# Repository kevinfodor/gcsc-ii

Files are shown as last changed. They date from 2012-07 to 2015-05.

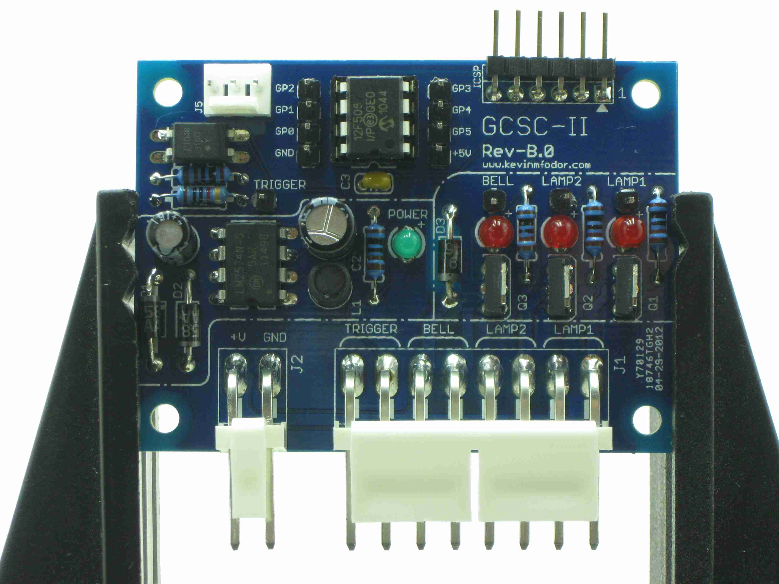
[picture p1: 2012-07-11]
images/gcsc-ii_pcb_assembled_sm.jpg

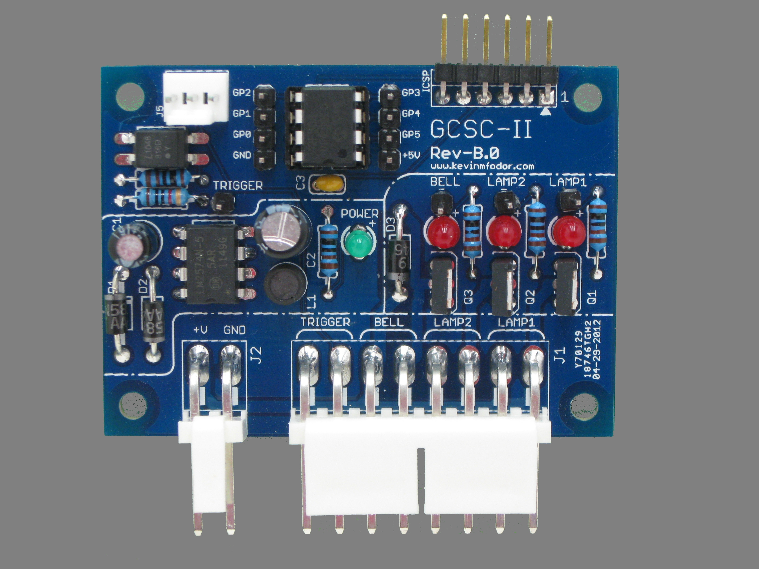
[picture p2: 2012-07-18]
images/wiki/gcsc-ii_pcb_front_grey.jpg

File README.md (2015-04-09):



This is a small embedded controller designed for the purposes of controlling an operating railroad crossing signal with 2 signal lamps and a bell. It was designed to work with a PVC based railroad crossing signal mast approximately 6-feet tall for display, demonstrations and overall amusement. I  have posted this design because I have been contacted by a few others who also saw my railroad crossing project and expressed a desire to build such a signal themselves. I hope this controller will be helpful to anyone who wishes to look at it.

This site contains all of the documentation, source code, schematic and PCB files necessary to build this controller (Rev.B). Please seek the Wiki for more details.

As a secondary goal, I also designed this board to be used as a PIC12 development board. The PCB silkscreen is well documented showing all the pin names and contains lots of holes for jumpers. The board can also be used directly with the PICKit3 programmer from Microchip via the ICSP header. It also has it's own 5V switching power supply on board. So basically all you need to do is provide power and your off and running.

In case your wondering about all the mention of "II" as in GCSC-II, this is a complete re-design of my earlier breadboard attempt found [here on my site](http://www.kevinmfodor.com/home/model-railroading-projects/railroad-crossing-signal). Much has changed since then. This is a very easy to build and very low-cost implementation of that control circuit.

I hope people find this useful. Please feel free to email me or contribute in anyway.

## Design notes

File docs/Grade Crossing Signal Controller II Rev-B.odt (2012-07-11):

# Grade Crossing Signal Controller II

Revision B

Requirements, Design and Implementation

Written By: Kevin Fodor

www.kevinmfodor.com

## Background

Recently someone was interested in my Railroad Signal Crossing Project (http://www.kevinmfodor.com/home/model-railroading-projects/railroad-crossing-signal) posted on my projects web site. He intends to build his own barrel-car train which will be able to pull around kids which should prove to be a huge amount of fun for them. Being of a train theme he was interested in constructing four grade crossing signals (crossbucks) presumably to lay about the area where the barrel cars would follow. Seing my project on my website he contacted me for more detailed plans on the construction of the signal post itself as well as the electronic controller for the lights and bell.

The physical construction went well and he made a great deal of improvements to make it easier to construct the signal itself. The electronics however were a bit more challenging. My original design was cobbled or hacked together as a work-in-progress. This means I didn’t set out to design anything. Just kind of put enough components together (wire-wrapped) and debugged the circuit till it worked. Consequently other than the schematic which documents the circuit, there is very little information on how to actually duplicate the circuit (wiring points, etc.). Of course my intent was never to make more than one one them anyway. Now that there is interest in making more than one, a better plan and approach is required.

## Purpose

This document will serve as a collection of objectives, requirements and design notes accumulated overtime to guide the re-design of this controller.

### Current Design Weaknesses

The re-design is aimed at making the controller simpler to build and more reliable among many other things. To address what improvements are to be made, below are the weaknesses I see in the existing controller desing;

- The existing design is wire-wrapped onto proto-board. This makes it very difficult to debug, copy and maintain as wires are fragile and break easily. Additionally, connection points are not easily observed.
- Overall the part count is rather high for what should be a very simple circult.
- The existing design uses a 556 (dual 555) timer to both trigger the signal (and control the on time) as well as the astable operation of the lights and bell. These devices are notoriously problematic and I have found often false trigger if great care is not observed. Additionally to obtain a square wave pulse (50% duty cycle) a diode is required, adding to the part count.
- The power output for the lights and bell are based on power transistors (TIP31 and TIP120). Although they appear to do the job, they are not very efficient and require drive transistors to operate them. They are also more difficult to use and generate significant heat while operating.
- The bell signal is derived from light flashing signal (derivative of the square wave using a diode, D2 and D3). This adds to the number of component required and complexity. More importantly however this also makes timing the bell “strike” time somewhat tricky as it is subject to the RC circuits (C9, R10) and (C10, R11). Along with the drive circuits, these parts are duplicated for each clock edge to trigger the bell.
- Separate transformers were needed since the bell being an inductive load tended to drop the supply voltage to the timer and other circuitry causing all sorts of “drop-out” problems. Transformers are expensive and it would be nice to require only one, and only if being powered by AC household line current. Each transformer also required a diode bridge to rectify the AC signal, duplicating those parts as well.
- The power supply is a linear one based on the LM7812 (Q1) which again is quite inefficient and not really suited to supply large currents to the lamps and bell.
- This board is a one-of-a-kind (sigh!) and making another is quite difficult (and expensive). If others would like to make them it is difficult to convey how to build it and to do so it would take some skill and patience.

## Design Goals

With the above listed and numerous weaknesses in mind, the following design goals are set in order to address them;

- The hardware design should use commonly available (free) tools which make the design open and accessible to others who may want to build and or modify the design further.
- Building a copy of the circuit should be simple, enabling many people of all kinds of skill level to build one. With this in mind a Printed Circuit Board (PCB) will be produced using through hole components.
- Overall part count to be reduced by 50%. Current design uses about 50 parts!
- Reduce overall cost to build. Current design costs $x to build.
- Trigger type and duration of signal operation shall be flexible (i.e. via software)
- Flash cycle time should be flexible (i.e. via software). However, as a baseline the previous design ran at 0.722 Hz with a 50% duty cycle (693 msec on/off) time so we will start with that.
- Bell Trigger time should be flexible (i.e. via software). Again since the previous design triggered the bell on each flash of the lamp, the bell will be triggered every 693 msec.
- Power stage should use more efficient power switching components (i.e. MOSFETs)
- Power supply shall be more efficient and provide enough power to lamps and bell (i.e. switching power supply)
- Software will control operation making it much more flexible to all users. Thus the controller will be based on a small and inexpensive microcontroller.
- Optional household AC or battery powered. This is due to the fact that unit may be used outdoors or where AC line current may not be available. In fact it is better to simply design the circuit to use DC power then add a AC->DC converter if needed.
- Learn something!
- Make it better!

## Block Diagram

The block diagram below shows the overall control circuit as a black box. What is inside the black box is what needs to be re-designed.

Illustration 1: Controller Block Diagram

## Physical Requirements

To meet the design goals set forth earlier, some physical requirements must be met;

1. Unit will be powered by a 12-VDC (nominal, 13.6 actual) battery
  a. Input power supply may vary between 9-VDC and 18-VDC and thus power supply should be tolerant of that.
  b. Target battery is a commonly available motorcycle/tractor battery (specs?)
    i. Consider small motorcycle battery with 3Ah capacity. High capacity are 14Ah capacity.
    ii. Power Wheels batteries are typically 9.5Ah SLAs.
    iii. 9V Duracell Copper Top, 10mA load over 50+ hours.
  c. Idle, quiescent current consumption should be less than 10mA.
2. Unit will include reverse polarity protection as to not blow out the controller if battery voltage is applied incorrectly.
3. Power supply will indicate operation using an LED.
4. Unit will be designed to anticipate being placed in a small enclosure (water resistant if used outdoors)
5. Must be able to independently control two automotive tail-light bulbs.
  a. May support either single or double filament bulbs
    i. Tail/marker Filament 12-VDC @ 0.5 A
    ii. Signal Filament 12-VDC @ 2.0A
6. Must be able to actuate a bell (Ace #36487 (http://www.acehardwareoutlet.com/productdetails.aspx?sku=36487))
  a. Note! This bell is a self-interrupting circuit as purchased. A modification must be made to the bell to allow it to work as a bell in this project and not as a “door-bell”. See Section 4 for more details.
  b. Bell is typically powered using three 6V DC batteries or AC-125C/36485 transformer (http://www.acefactorystore.com/proddetail.asp?prod=36485) (Output: 8 VAC-10 VA, 16 VAC-10 VA, 24 VAC-20 VA).
7. Must be triggered by a momentary switch.
8. Support a low-power mode when not in operation.
9. Diagnostic LEDs should be included for each lamp and bell to verify operation if such devices are not connected.
10. PCB and wiring harness should use commonly available wire-to-wire connectors suitable for outdoor environments.

## Functional Requirements

The unit has very few functional requirements. Those requirements are detailed below.

1. Trigger – Actuates the grade crossing signal controller, causing lights to flash and bell to ring along with general amusement by all.
  a. Momentary actuation via push button or make/break connection.
  b. Toggles signal on/off
    i. Press once to turn on, press again to turn off
      1. Maximum on time is 30 seconds (timeout)
    ii. Hold for continuous operation (> 2 seconds)
      1. No timeout (forever).
      2. Turn off if pressed again.
2. Lamps (2)
  a. 12-VDC Automotive Taillight Lamps (0.5/2.0 Amps)
  b. Flash at an approximate 2/3 second rate, 50% duty cycle.
3. Bell
  a. 12-VDC Door Bell (modified, 2-3 Amps peak pulse driven)
  b. Strike bell in sync with each lamp flashing
  c. Strikes are generated by short pulse to bell.

## Trigger Design

The trigger is the only control input into the signal controller. It provides several functions although it is only a single momentary switch. To adequately define this behavior it is often helpful to develop a finite state-machine.

Modes: Active (Timeout, Continuous), Inactive

## Stock Bell Modifications

The signal’s bell which is to be used is a commonly available door-bell (Ace #36487 (http://www.acehardwareoutlet.com/productdetails.aspx?sku=36487)) available at most hardware stores. The bell, as it comes stock in the package is actually made from an electromagnet which is used to operate a self-interrupting circuit (http://home.howstuffworks.com/home-improvement/repair/doorbell2.htm). This is useful when operated from a line transformer (as is intended), but for our purposes the controller circuit will be actuating the bell instead through a short pulse. To do this, we will need to modify the bell slightly.

Here is an illustration of the door-bell as it is provided. Understanding its operation as a self-interrupting circuit is helpful so that we can understand how to modify it properly.

A C B

When electromagnet

is not engaged circuit

is complete

Illustration 2: Door bell (unmodified) when circuit is closed.

One end of the electromagnet wire is connected directly to one end of the electrical circuit (terminal-C). The other end of the wire connects to a metal contact, which is adjacent to a moving contact arm or clapper (terminal-A). The clapper is a thin piece of light, conductive metal. The anchored end of the clapper is wired to the battery (terminal-B). When the electromagnet is turned off (Illustration 2 above), the free end of the clapper rests against the contact point (terminal-A). This forms a connection between that end of the wire and the electrical circuit. In other words, electricity can flow through the electromagnet when the circuit is closed (terminal-A and B are connected).

A C B

Bell strike when electromagnet

is engaged, but circuit is broken

releasing the arm again

Illustration 3: Door bell (unmodified) when circuit is open

Initially, the electromagnetic field attracts the clapper off the stationary metal contact (terminal-A). This breaks the connection between the circuit and electromagnet, so the electromagnet shuts off (Illustration 3 above). Without a magnetic field pulling it back, the clapper snaps back into position against the stationary contact (terminal-A). This reestablishes the connection between the electromagnet and the circuit, and the current can flow through it again. The magnetic field draws the clapper up, and the process repeats itself as long as you apply power from the battery. In this way, the electromagnet keeps shutting itself on and off. The ringing sound you hear is the sound of the rapidly moving clapper hitting the bell dozens of times a second.This is the same system used in old-fashioned fire alarms and school bells.

This is all very interesting but it is not the behavior we want. What we want is to be able to control the bell enough to achieve a single strike of the bell each time a lamp is turned on. To do this we need to modify the stock door bell so that it is now a non-interrupting circuit. The single strike will instead be controlled by our controller.

A C B

add jumper

Illustration 4: Door bell (modified) as a non-self interrupting circuit

In Illustration 4 above we can see that by adding a jumper between terminal-A and terminal-B we effectively disable the self-interrupting part of the circuit. Now applying the power source to the circuit causes the clapper to strike the bell. Keep in mind with this modification, as long as power is applied, the electromagnet is engaged and the bell is struk. The clapper arm will not move away from the bell until the power source is removed. It is this operation that our controller is responsible for. The controller must be able to apply the power source to the circuit as a quick pulse, just enough to ring the bell once and then disengage. To determine just how long to pulse the circuit was unknown, so a test circuit needed to be designed.

## Bell Driver Test Circuit

The bell driver portion of the design was always the most troublesome for me, so let's start there. Once we have that designed the rest should be a piece of cake.

The bell we are going to design the output circuit for is an Ace #36487 (http://www.acehardwareoutlet.com/productdetails.aspx?sku=36487). It consists of an electromagnet (coil) which must be stimulated with a voltage to make the arm move. The moving arm is attached to a long clapper, which rests alongside a circular bell. When the arm is moved (current applied) it strikes the bell. When current is removed the arm moves away from the bell (snaps back) ready to strike again.

The specs on the door-bell state that it can be driven with three 6V DC batteries (18 VDC) or AC using the 125C/36485 transformer. Since our controller uses DC voltage (supplied by a 12 VDC battery) we will use 12 VDC to drive the bell. It has been found that the bell can be adequately driven using 12 VDC.

Moving the arm with the electromagnet is problematic because it is what is known as an inductive load. So some extra considerations need to be made when driving an inductive load versus and purely resistive one (such as a lamp). One thing to note is that the coil resistance at steady state is approximately 3-4-ohms. At steady state, with 12 VDC applied, this means the current through the coil would be as high as 4 amps. That also means the bell could draw as much as 36 watts! That is a significant amount of power. With power comes heat, and if you apply that current for too long the bell's coil will burn out.

Fortunately for us we actually don’t want to drive the bell’s coil with a steady current. In fact doing so would slam the arm against the bell and keep it there. There would not result a “free ringing” sound and instead it would be muffled by the arm resting against the bell. Instead we want a quick, bright ring when we trigger it. We can do this by driving a short pulse into the bell.

So how long should the pulse be? What will be the current through the bell during that time?

To answer this we need to experiment. A sample test circuit to determine this was constructed as in Illustration 5. This circuit allows me to send a pulse (from a microcontroller) into the bell driver circuit and view on an oscilloscope how much current is going through the bell. Current is measured across Rref which is a 1Ω 10-Watt Power resistor.

Illustration 5: Bell Coil Driver Test Circuit

To stimulate the bell, I drive a periodic (1-second) pulse of approximately 10 msec in width through the coil. Probing across Rref shows the current through the 1Ω resistor. At this point the math is easy as we simply use V = I*R given Rref = 1Ω, we then know the voltage is equal to the current through the resistor V=I.

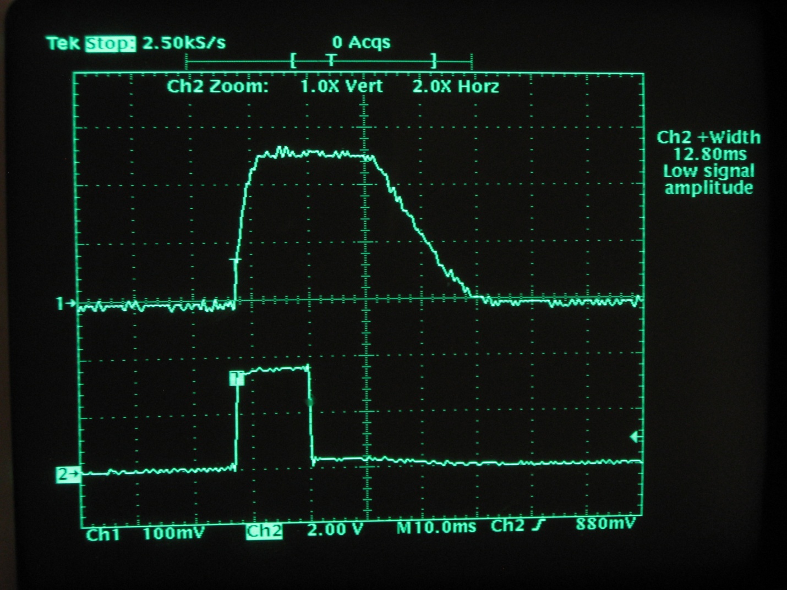
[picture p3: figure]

Illustration 6: Experimental Bell Driver Test Circuit Trace

The trace is shown above in Illustration 6 as seen on the oscilloscope. The microcontroller generates a 12.80 msec pulse to drive the opto-isolator which drives the MOSFET gate. The current through the coil is the same as that which is through the MOSFET drain-source and the Rref resistor. As can be seen from the trace, The initial current starts at 0 and increases exponentially to 2.6-Amps, after about 4 msec reaches steady state, and then about 25 msec after the pulse goes low it begins to exponentially decrease back to 0 amps after about 43 msec total.

To simplify let’s just assume with an approximate 10 msec pulse, the device sees full current for 50 msec every 700 msecs. Also recall that the 1Ω resistor, Rref won’t be in the actual drive circuit (it was only used for these measurements), so we have to assume the maximum current which we have seen at 12V, steady state which is about 2.75 A.

With this information we then know that at 12 VDC, the bell sees 2.75A for less than 10% of the time. This is worst case scenario and will serve as guidance into our design process for the bell driver.

## Basic Design Elements

The overall circuit consists of 4 basic sections or elements which are 1) High Power Output Stage, 2) The Controller 3) Trigger and 4) Power Supply. Each of these elements are addressed below.

### High Power Output Stage

The high power output stage needs to drive two lamps and a bell. So we need three separately and digitally controlled high-power output control circuits. Since the microcontroller will be controlling and thus driving each circuit, the circuit must be controllable using a +5V signal. We also must consider power dissipation of the control circuit itself. We are switching (worst case) 2A of current to each lamp. Designs for the lamps and bell will be addressed separately below.

Often the first solution a design reaches for when needing to switch high power loads with a microcontroller or other small voltage and current device is a relay. However relays are notoriously unreliable in an outdoor environment, involve mechanical parts and will require drive circuitry of its own anyway since a microcontroller cannot on it's own drive the relay's coil.

Another approach is to use bipolar transistors. This is the approach I took on my first design (http://7450666183147974826-a-1802744773732722657-s-sites.googlegroups.com/site/kfodorprojects/home/model-railroading-projects/railroad-crossing-signal/Visio-C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) using a TIP31 (http://www.fairchildsemi.com/ds/TI/TIP31A.pdf) for the lamps and Darlington TIP120 (http://www.fairchildsemi.com/ds/TI/TIP120.pdf) for the bell. It also required a small NPN transistor to drive each of them. In total 16 parts (resistors and transistors) were needed to implement the circuit. Furthermore these transistors are current controlled devices requiring a significant base current to turn them on. Additionally the lowest attainable on-state voltage drop is determined by the collector-emitter saturation voltage VCE(SAT), which for the TIP31 VCE(SAT) = 1.2 V when IB = 375mA, while the TIP120 VCE(SAT) = 2.0 V when IB = 12mA. Power dissipation (which is converted to heat) is determined by P = VI so the heat generated by the part is subject to this VCE(SAT) parameter. Using the TIP31 to drive a 2A lamp results in a best case power dissipation of 2.4 watts (a 0.5 A load dissipates 0.6 watts). That best cast occurs when driving the base with 375 mA. A TO-220 package has a typical thermal resistances of TR(j-c) = 3 ºC/W and TR(c-a) = 62.5 ºC/W. Thermal resistance is an important parameter because it determines how high the temperature of the device will rise when dissiping an amount of power. Of specific importance here is the device's junction temperature (Tөj), which for the TIP31 cannot exceed 150 ºC. Plugging those values into the basic device thermal characteristic equations is as follows;

T_"R(j-a)" = T_"R(j-c)" + T_"R(c-a)" = (3 + 62.5) %degree C/W = 65.5 %degree C/W
newline
newline
T_rise = T_"R(j-a)" cdot P_D = 65.5 %degree C/W cdot 2.4 W = 157.2 %degree C
newline
newline
T_rise = T_"R(j-a)" cdot P_D = 65.5 %degree C/W cdot 0.6 W = 39.3 %degree C

Woah! At an ambient temperate of 25 ºC the 2A lamp causes the TIP31 junction temperature to be about 182.2 ºC (360 ºF). That is 32.2 ºC above the maximum. The 0.5A lamp will make it about 64.3 ºC (148 ºF) which is within the limits. So, the 2A load is simply not possible (the transistor will blow) and the 0.5A load is still pretty hot. I am glad that this transistor is on only half the time! I have noticed that in the original prototype circuit these lamp drive transistors were pretty hot at the 0.5A load, I never tried a 2A load. Glad for that!

For the re-design I chose to use MOSFETs. MOSFETs are great for switching high currents because they are voltage controlled devices and if driven properly have a very low “on” resistance known as RDS(ON). Low “on” resistance means more efficiency, less power dissipation and therefore less heat. There are other choices as well (i.e. IGBTs for instance) but I decided on MOSFETs since much of this work would also be a basis for other work I would like to do in the area of motor controllers. So I went with MOSFETs.

There are some important considerations to take into account when driving MOSFETs however. One is the gate drive voltage, VGS, the other is switching speed.

MOSFET based power designs can gain additional efficiency by properly matching the gate drive voltage VGS with the MOSFETs being driven. Driving a MOSFET gate with a higher voltage, results in lower on-resistance, RDS(ON). However we cannot drive the MOSFETs with too high of a gate voltage without requiring additional drive (level translation) circuits which again add cost (the BOM) and complexity (the PCB layout). Higher gate drive voltage levels place additional charge into the gate-to-source junction of the MOSFET, resulting in increased losses within the MOSFET driver stage. To increase efficiency the applied voltage should drive the MOSFET gates such that the added gate charge and switching losses are less than the power savings gained by lowering the RDS(ON).

Higher gate drive results in higher switching losses when used at higher frequencies, switching losses dominate in which case a lower VGS would be preferred. At lower frequencies, where conduction losses dominate, a lower RDS(ON) is preferred, and higher VGS is desired. The consideration for switching speed is not really an issue in this application. The lamps are not driven faster than being turned on or off every 0.7 seconds ( < 1.5 Hz). The bell is switched on and off a bit faster, but infrequently, once every 0.7 seconds it is switched on for 10 msec then switched off. Even if this were continuous it would only be at a rate of about 100 Hz. At those frequencies switching speed really is not significant. It usually isn't a factor with MOSFETs till we start talking about several kHz switching speeds.

In this application, the controller has a 5V output so ideally being able to drive a MOSFET at a VGS of 5V is desired.

Another consideration is weather to use a low-side or high-side driver configuration.

A low side driver is implemented with the switch (N-Channel MOSFET) between the device being controlled and ground. A high side driver is implemented with the switch (P-Channel MOSFET) between the +V supply and the device. These two types are shown below.

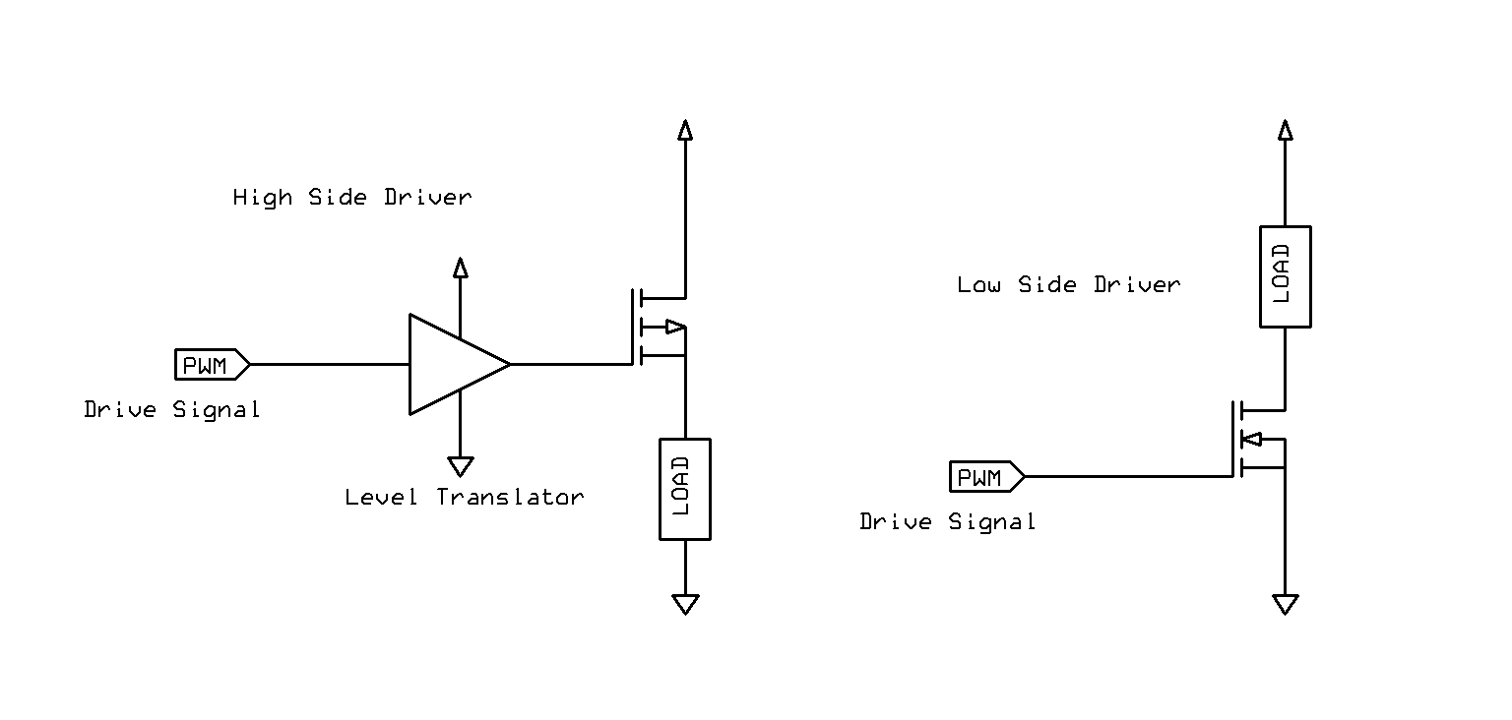
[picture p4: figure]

Illustration 7: Comparison of High-Side and Low-Side Drivers

Low-side drivers in some applications are considered somewhat “less safe” because the device has voltage on it even when turned off. For instance, what is someone cuts the cable or damages the device and it shorts to ground. Additionally since the load is hot, it can be turned on without the controller by connecting the opposite side to ground. If this were a motor for instance, the motor could be accidentally turned on.

High-side drivers are preferred from a robustness and sometimes safety perspective. This is particularly important when the device being driven is not near the controller. When the high-side driver is off, the device is at ground potential, with little or no current flow. However, high-side drivers are somewhat more complex to implement and require more components (i.e. drivers, level translators), especially when the logic level driving them doesn't match the driver voltage.

In this case a low side driver was implemented for its simplicity and reduced complexity (shown below). The driver (without LED state indicator) consists of only two parts. The MOSFET, Q switch and bleeder resistor RB. An LED diode, D and current limiting resistor RA were added to given visual indication of the switch state which is helpful during development and troubleshooting. It also allows the circuit to be useful even without a load connected to the output.

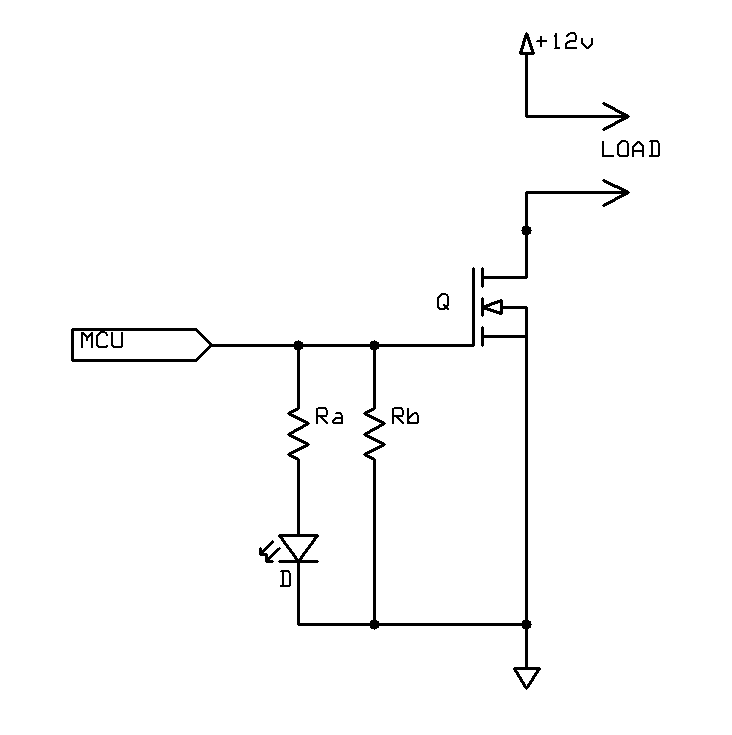
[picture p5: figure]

Illustration 8: Basic Power Output Low-Side Driver Circuit Design

The bleeder resistor, RB is used to bleed off current from the MOSFET gate when not being driven. A MOSFET gate acts much like a small capacitor which can leave a charge (and thus leave the switch on) when not being driven. A value of 100kΩ was chose for this resistor which draws a maximum of 50µA. In fact the bleeder resistor is probably not even needed in this application since it is connected to a microcontroller output pin. A bleeder resistor is only really needed when the input maybe left floating.

Note: I plan on removing the bleeder resistors in the next revision of the board.

The indicator circuit made up of a red LED, D (SSL-LX5093HD) and current limiting resistor RA = 1kΩ sets the LED current at about 3 mA due to the LED's forward voltage drop of VF = 2 V. See Section 'Power Supply Design' below. This is sufficient current to drive the LED.

MOSFET Q was selected as an On-Semiconductor NTD4906N-1G (http://www.onsemi.com/pub_link/Collateral/NTD4906N-D.PDF) N-Channel Power MOSFET. The characteristics of this MOSFET are low RDS(ON), low gate capacitance and relatively small through-hole package (IPAK). At $0.26/ea they are very inexpensive.

Absolute Maximum Ratings at TA = 25ºC

VDSS = 30 V

VGS = +/- 20 V

ID = 10.3 A (continuous, no heatsink or pad)

PD = 1.38 W

TӨj = 175 ºC

Electrical Steady State Characteristics

RDS(ON) = 7 mΩ at VGS = 4.5 V

RDS(ON) = 6 mΩ at VGS = 5.0 V

TӨ(j-a) = 109 ºC/W

It would be perhaps considered “better-design” to have implemented a high-side driver instead. But its not like we are dealing with big heavy motors here. So I went with the simpler design approach.

### Lamp Output Stage Design

Note: Most automotive trailer bulbs have two terminals each connected to a different filament. One for turn signal (green wire) and another for taillight (brown wire). They are both referenced to the chassis ground or frame via a bolt. The turn signals draws approximately 2A while the taillight draws 0.5A. I have used both terminals and obviously one is significantly brighter than the other. Since this is likely to be used outdoors, the brighter one is considered in the design. Also since this would also represent the worst case scenario, the 2 A filament is used for that reason as well.

Using ID = 2 A, and TӨ(j-a) = 109 ºC/W we calculate power dissipation, junction temperature rise and expected junction temperature in ambient conditions TA = 25 ºC.

P_D = I_D ^ 2 cdot R_"DS(ON)" = (2A)^2 cdot 0.007%OMEGA = 0.028 W = 28 mW
newline
newline
T_rise = T_{%THETA(j-a)} cdot P_D = 109 %degree C/W cdot 0.028 W = 3.052 %degree C
newline
newline
T_{%THETA j} = T_a + T_rise = 25 %degree C + 3.052 %degree C = 28.052 %degree C

Both power dissipation, PD = 28 mW and junction temperature TӨj = 28 ºC (83 ºF) are well below this MOSFETs maximum ratings, PD(max) = 1.38 W and TӨj(max) = 175 ºC. These results are also much better than the original transistor based design.

### Bell Output Stage Design

Using ID = 2.75 A, and TӨ(j-a) = 109 ºC/W we calculate power dissipation, junction temperature rise and expected junction temperature in ambient conditions TA = 25 ºC.

P_D = I_D ^ 2 cdot R_"DS(ON)" = (2.75 A)^2 cdot 0.007%OMEGA = 0.05294 W = 52.94 mW
newline
newline
T_rise = T_{%THETA(j-a)} cdot P_D = 109 %degree C/W cdot 0.053 W = 5.77 %degree C
newline
newline
T_{%THETA j} = T_a + T_rise = 25 %degree C + 5.77 %degree C = 30.77 %degree C

Both power dissipation, PD = 53 mW and junction temperature TӨj = 30.77 ºC (87.39 ºF) are well below this MOSFETs maximum ratings, PD(max) = 1.38 W and TӨj(max) = 175 ºC.

This circuit is identical to the lamp output stage expect for the fact that a “freewheel, flyback, or snubber diode (http://en.wikipedia.org/wiki/Flyback_diode)” is needed in a reverse biased direction across the bell's coil. This helps to eliminate the sudden voltage spike seen across an inductive load when its supply voltage is suddently removed. When the device rapidly turns off, the diode becomes forward biased and the collapse of the energy stored in the coil causes a current to flow through the freewheel diode. Without this protection in place high currents would occur causing a high voltage spike or transient to flow around the circuit possibly damaging the switching device. This freewheeling diode conducts this voltage spike, effectively shorting the coil, protecting the MOSFET switch. The diode absorbs the energy (power) dissipating it out of the coil, for this reason the diode needs to have a high enough power dissipation capability to adequately absorb the power when the switch is turned off.

Generally you need a diode with a high surge current capability to provide this protection. A 1N4007 (http://www.fairchildsemi.com/ds/1N/1N4001.pdf) general purpose rectifier is used to provide this protection. The 1N4007 is very common diode (only $0.09 ea) and has specifications such as IFSM = 30A, VRRM = 1000V and VF = 1.1V.

Note: A faster diode such as the popular 1N5819 may be desired although it has a much lower VRRM of about 40V. However since we are interrested in surpressing spikes and not a constant reverse voltage these may work fine. Schottkey diodes are optimized for very low voltage drop, and fast operation. The 1N5819 (http://www.fairchildsemi.com/ds/1N/1N5819.pdf) features a maximum PD = 1.25 W, IFSM = 25A, and VF of 0.6V

### The Controller

The functional requirements of this project are very simple and thus some might argue a microcontroller is overkill. That may be true, but simple microcontrollers these days are very inexpensive, easy to use and much more flexible than their discrete hardware equivalent implementation (i.e. 555 timer, oscillating comparators, RC-circuits, etc). Also writing a few lines in software which could in turn be easily modified, enhanced or completely re-purposed might be beneficial to someone. For these reasons, a microcontroller was chosen opposed to discrete hardware to implement the controller logic.

There are countless controllers on the market and many of which are very low-cost, low-power and have more than enough RAM, ROM and I/O resources to meet this very simple application’s needs. However we need to start somewhere. To start we need to derive the basic controller requirements (define resources). These resource requirements are derived from Section - Functional Requirements and are listed below;

- 5V Supply
- 1 Input (switch)
- 3 Outputs (bell-1, lamps-2)
- 1 Time Base (for timers)
- ROM (< 256 bytes) - estimated
- RAM (< 64 bytes) - estimated

Hundreds of microcontrollers meet these requirements. The first step in narrowing down the choices might be to narrow down a vendor. I have familiarity working with Freescale, TI and Microchip controllers to name only a few. Each of those vendors offer now end controllers more than capable of meeting this application's resource requirements. The Freescale stuff I have worked with in the past have been in the HC908-QT/QY family which is largely outdated at this point, not a good choice for new designs.

TI also has an insanely inexpensive and convenient TI MSP430 LaunchPad (http://processors.wiki.ti.com/index.php/MSP430_LaunchPad_(MSP-EXP430G2)). The TI LaunchPad is an easy-to-use development tool intended for beginners and experienced users alike for creating microcontroller-based applications. At $4.30, the LaunchPad offers everything you need to get started with your projects. Indeed it does! You get a development board with LEDs, Pushbuttons, a microcontroller(MSP430G2231 (http://www.ti.com/product/msp430g2231)) and debugger. How can you go wrong? Plus this project will then provide a simple introduction to using this controller and platform, which would meet my goals of actually learning something new. However the down side is this platform runs on 3.3V supply. Although it could be made to work, we really need 5V going to our MOSFETs (see above section). So something else is needed.

Enter Microchip, if for no other reason, I have this handy PicKit3 debugger/programmer (http://www.microchip.com/stellent/idcplg?IdcService=SS_GET_PAGE&nodeId=1406&dDocName=en538340) and demo board I really have not had the opportunity to try. Plus I really have not given Microchip components much of a try either, so it would be interesting to see what they offer. Microchip also offers a free set of development tools, the MPLAB X IDE (http://www.microchip.com/stellent/idcplg?IdcService=SS_GET_PAGE&nodeId=1406&dDocName=en019469&redirects=mplab) which will suit me fine. Again, something free and new to learn...all systems go.

So what do they have? A parametic search of what they have available via their product selector (http://www.microchip.com/productselector/MCUProductSelector.html) yields 25 parts which are 8-bit architecture and up to 8-pins all in their PIC12F family of parts. Off to Mouser (http://www.mouser.com/Semiconductors/Integrated-Circuits-ICs/MCU-MPU-DSP-DSC-SoC-Processors/Microcontrollers-MCU/_/N-94a4nZscv7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) and of the PIC12F family of parts with a PDIP-8 package (because we want it easy to solder and prototype) we find those same 25 parts (http://www.mouser.com/Semiconductors/Integrated-Circuits-ICs/MCU-MPU-DSP-DSC-SoC-Processors/Microcontrollers-MCU/_/N-94a4nZscv7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). So which is the cheapest? At $0.79 for a single unit, the PIC12F508-I/P (http://ww1.microchip.com/downloads/en/DeviceDoc/41236D.pdf) is the winner.

The PIC12F508 features the following:

- 4-MHz operation with internal precision oscillator
- In-Circuit Serial Programming (ICSP) and In-Circuit Debugging (ICD) Support
- Power-On Reset (POR)
- Internal Weak Pull-Ups on I/O Pins
- Wake-up from Sleep on Pin Change
- Wide Operating Voltage Range: 2.0V to 5.5V
- 6 I/O Pins:
- 5 I/O pins with individual direction control
- 1 input only pin
- High current sink/source for direct LED drive
- Wake-on-change
- Weak pull-ups
- 8-Bit Real-Time Clock/Counter (TMR0) with 8-Bit Programmable Prescaler
- 512 Words of FLASH
- 25 Bytes of SRAM

This should more than meet the resource requirements of the controller. The other nice thing is that if at some point in the future I decide I need more RAM and/or FLASH all of the parts in this family are pin-compatible. Specifically the PIC12F1840-I/P (http://ww1.microchip.com/downloads/en/DeviceDoc/41439A.pdf) at $1.41 would be a suitable drop-in replacement at the higher end of the memory resources availabile with 256-bytes of RAM and 7K of FLASH in case my original estimates are wrong.

The pin-out of the PIC12F508 is as shown below. Minimal connections are required as nothing special is required beyond a stable power supply (5V) connected between VDD and VSS.

Illustration 9: PIC12F508 Pinout Diagram

Pin assignments are assigned as follows (TRIS Register):

MCU Pin | Pin # | Function | Feature
GP0/ICSPDAT | 7 | Output | Lamp-1
GP1/ICSPCLK | 6 | Output | Lamp-2
GP2/T0CKI | 5 | Output | Bell
GP3/MCLR/VPP | 4 | Input | Trigger
GP4/OSC2 | 3 | Output | Unused
GP5/OSC1/CLKIN | 2 | Output | Unused

Note this leaves us with 2-unused pins which may be re-purposed later. For now they will be designated as outputs driven low (unused). Note PIC® Microcontroller Low Power Tips ‘n Tricks (http://ww1.microchip.com/downloads/en/devicedoc/01146b_chapter%202.pdf) TIP #3 Configuring Port Pins states “If a port pin is unused, it may be left unconnected but configured as an output pin driving to either state (high or low)...” and “There is no additional current consumed by a digital output pin other than the current going through the pin to power the external circuit.”. Therefore leaving the pin unconnected should not consume any additional current.

The input trigger was assigned to GP3 because GP3 can be used as an input only. Since the functionality of this pin is limited, it makes sense to assign it to the trigger. GP3 can also be configured for “wake-up on change” which can be useful when implementing low-power modes of the MCU.

Device DC Electrical Characteristics

Voltage on VDD with respect to VSS ...........................................................................................................0 to +6.5V

Voltage on MCLR with respect to VSS.......................................................................................................0 to +13.5V

Voltage on all other pins with respect to VSS .......................................................................... -0.3V to (VDD + 0.3V)

Total power dissipation .................................................................................................................................800 mW

Max. current out of VSS pin .............................................................................................................................200 mA

Max. current into VDD pin ...............................................................................................................................150 mA

Input clamp current, IIK (VI < 0 or VI > VDD).............................................................................................+/-20 mA

Output clamp current, IOK (VO < 0 or VO > VDD) ...................................................................................+/- 20 mA

Max. output current sunk by any I/O pin ............................................................................................................25 mA

Max. output current sourced by any I/O pin ........................................................................................................25 mA

Max. output current sourced by I/O port .............................................................................................................75 mA

Max. output current sunk by I/O port ..................................................................................................................75 mA

DC Characteristics of the Inputs and Outputs

The PIC12F508 will recognize a high state when the input is between 2.0V → VDD. It will recognize a low state when the input is between VSS → 0.8V.

When configured as an output a pin set to high the voltage observed will be a minimum of VDD – 0.7V. Set to low state the output voltage observed will be a maximum of 0.6V.

PicKit3 ICSP and ICD support

As the datasheet indicates the PIC12F508 supports both In-Circuit Serial Programming (ICSP) important for programming the chip with software, and ICD (In-Circuit Debugging) important for development and debug. However to get the ICD to function an additional “header” is needed. I don't know much about that “header” so since this software is very basic, I am hoping will not need it.

ICSP however is important, at least on a prototype or breadboard. This allows new software to be programmed into the MCU. It is not needed for normal operation. However it is convenient (and common practice) to at least layout the PCB with pins that can be populated with a header so that a ICSP can be inserted and program the device using the PCB rather than relying on some external programming board. For this reason the ICSP pins will be on the PCB but may be unopulated if this capability is not needed or desired (cost).

Microchip provides a very handy “poster” which simplifies undertanding of how to connect the ICSP pins to the microcontroller. It can be found here (http://ww1.microchip.com/downloads/en/DeviceDoc/DS-51792B.pdf).

To summarize the connections on this PCB will be connected to the 5 pins of the PicKit3 via a 6-pin 0.1” pitch header as follows:

MCU Pin | MCUPin # | PicKit3 Pin# | PicKit3 Function
VSS | 8 | 3 | Vss Ground
GP0/ICSPDAT | 7 | 4 | PGD (ICSPDAT)
GP1/ICSPCLK | 6 | 5 | PGC (ICSPCLK)
GP2/T0CKI | 5
GP3/MCLR/VPP | 4 | 1 | MCLR/VPP
GP4/OSC2 | 3
GP5/OSC1/CLKIN | 2
VDD | 1 | 2 | VDD Target

Note: PicKit3 Pin #6 (PGM(LVP)) is not need and thus not connected.

Microchip offers a handy document entitled In-Circuit Serial Programming (ICSP) Guide (http://ww1.microchip.com/downloads/en/devicedoc/30277d.pdf) which details how designers should incorporate this capability in their designs. The section How to Implement ICSP Using PIC12C5XX OTP MCUs on page 13 (TB017) is particularly useful which outlines the following;

During the initial design phase of the application circuit, certain considerations have to be taken into account (snap! if I only read that earlier). In order to implement ICSP on your application board you have to put the following issues into consideration:

1. Isolation of the GP3/MCLR/VPP pin from the rest of the circuit.
2. Isolation of pins GP1 and GP0 from the rest of the circuit.
3. Capacitance on each of the VDD, GP3/MCLR/VPP, GP1, and GP0 pins.
4. Interface to the programmer.
5. Minimum and maximum operating voltage for VDD.

Specifically points 1 and 2 above regarding isolation are particularly important. In this design GP3 is already sufficiently isolated since when the switch (trigger) is not pressed the output transistor is high impedence to ground and the only connection to GP3 is a pull-up resistor R2. GP1 and GP0 however should have isolation points which allow them to be driven by the programmer only when the ICSP mode is used.

Note: Unfortunately in the first design I did not consider this. In the next revision I plan to separate the ICSP portion of the design which can be more easily isolated and separated from the main circuit design. The ICSP implementation in this revision does work as long as the MOSFETs are not connected (particularly Q2).

MCU Configuration

The MCU Configuration shall enable the following via the __CONFIG() keyword;

OSC_IntRC – Use internal RC oscillator

WDT_OFF – No watchdog timer, disabled

CP_OFF – Code Protection is off

MCLRE_OFF – Don't use master clear reset function on GP3, disabled

The MCU OPTION Register value will be a value of 0xD7 described as follows;

OPTION = 0b11010111;
//1------- Wake-up on pinchange disabled. (GPWU=1)
//-1------ Weak pullups disabled. (GPPU=1)
//--0----- T0CS, use internal instruction cycle clock Fosc/4
//---1---- T0SE, don't care.
//----0--- Prescaler assigned to TMR0 (PSA=0)
//-----111 Prescaler 1:256 (PS=111) 256 usec

Note: Initially I didn't bother using the low-power mode of the MCU or enable the use of “wake-up on change”. That is something which can be expirimented with and added later.

Timer Configurations and Calculations

The internal precision oscillator will be used to reduce overall part count and cost. The internal oscillator operates as 4-MHz (FOSC). There are 4-cycles required per clock tick so the rate at which instructions run is 1-MHz (FOSC/4). Since the 1:256 timer prescaler is configured (see above) this means our timer will increment once every 256 usec, known as a clock tick.

t_clock = {Prescaler cdot 1000000 usec} over {{F_OSC}over{4}} = 256 usec

For convenience our timer 'tick' should occur once every 10 milliseconds. So to get milliseconds from tclock, we calculate tcount as follows.

t_count = {10000 usec} over {t_clock} = 39

Back calculating the actual tick our application will experience using this timer we find that using following:

t_tick = t_count cdot t_clock = 9984 usec = 9.984 msec

This ends up being about a -0.16% error which is pretty good. But since we now know what ttick is, we can use that to compute things like;

lamptimeout = 0.7 seconds, lampcount = 70, error = -0.16%

lamp_count = floor[{0.7 sec cdot 1000000 usec/sec} over {t_tick}] = 70

activetimeout = 30 seconds, activecount = 3004, error = -0.0269%

active_count = floor[{30 sec cdot 1000000 usec/sec} over {t_tick}] = 3004

lpresstimeout = 2 seconds, lpresscount = 200, error = -0.16%

lpress_count = floor[{2 sec cdot 1000000 usec/sec} over {t_tick}] = 200

The timer is RESET by writing a 0 to the TMR0 register and expires when the TMR0 register is read and is equal to tcount (39). Thus the basic “super-loop” pseudo code is as follows;

START

FOREVER

{

// Wait for timeout (~10 msec)
while (TMR0_COUNT != TMR0);
TMR0 = 0; // Reset timer

// Do some work...

}

END

The above “super-loop” runs every 10 msec.

### Trigger

To trigger the signal an SPST switch (or other suitable contact) is used to indicate the signal is to turn on. There are many ways to interface external inputs into a micro-controller. I have written a bit of a survey of various input protection techneques and concepts in my post; Microcontroller Input Protection Techniques (http://www.kevinmfodor.com/home/My-Blog/microcontrollerinputprotectiontechniques) which can be referenced for more detailed information on that subject.

Based on how this controller is intended to be used (outdoors, uncertain environments) I decided it would be best to use optical isolation as an input interfacing and protection techneque. This techneque obviously uses an optoisolator (http://en.wikipedia.org/wiki/Opto-isolator) and that implementation is described in the following section.

Below is a simple implementation of an optoisolated switch input. Notice the output of the optoisolator is configured in “pull-up” mode, meaning when the output transistor is off, the output is high (VDD = 5V) and the MCU input sees this as a logical “1”. When the output transistor is on, the output is low (ground) and the MCU sees this as a logical “0”. To turn the transistor on, the input LED must be driven by the switch input which happens when the switch is closed. The LED's cathode lead is driven to ground, completeing the circuit from VDD (5V) through RF to ground. From the MCU software perspective, a press is indicated by a logical “0” and not pressed by a logical “1”.

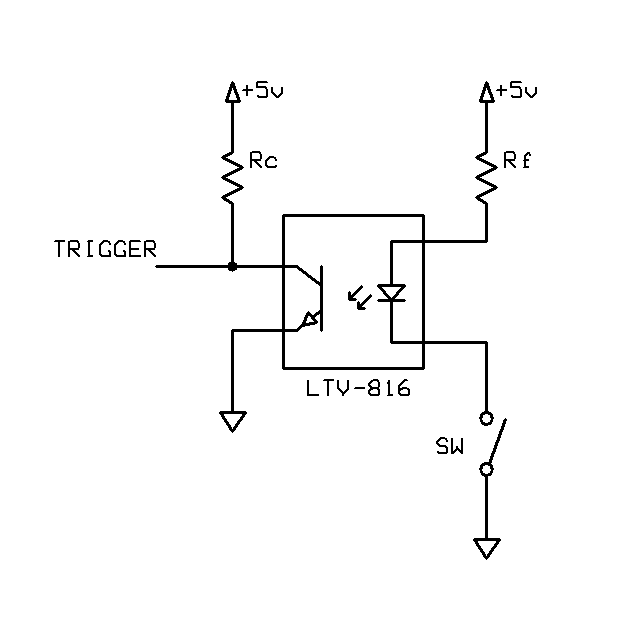
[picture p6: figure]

Illustration 10: Optically Isolated Input

The nature of the pushbutton trigger switch lends itself very well to be interfaced to the MCU through an optoisolator. The speed of the optoisolator is not critical since the pushbutton cannot be pressed very fast anyway. Therefore virtually any single channel optoisolator will do. Due to cost ($0.18/ea) and availability I chose the Lite-On LTV-816 (http://www.mouser.com/catalog/specsheets/LTV-8x6.pdf).

The relevant specifications of this part are as follows:

Absolute Maximum Rating (TA = 25ºC)

Input: Forward Current (IF) = 50ma max

Input: Reverse Voltage (VR) = 6V

Output: Collector Current (IC) = 50mA max

Output: Collector-Emitter Voltage (VCE) = 80V max

Isolation Voltage: 5 kVRMS max

The isolation voltage means that it can effectively isolate up to 5 kVRMS on the optoisolators input into the MCU (sufficient for a nearby lightning strike, electostatic discharge (ESD), etc.). Also the parameter VR indicates the input can tolerate a reverse voltage of maximum 6 V, so if someone applies something other than ground to the input it can tolerate up to 11V (11V – 5V = 6 V). In which case only the optoisolator may blow, the MCU will still be protected.

Electrical/Optical Characteristics

Input Forward Voltage (VF) = 1.2V (@ IF = 20ma)

We would like the output of the optoisolator's transistor to be well in saturation with minimal forward current (IF). We also need to make sure the transistor's output can provide enough current to drive the MCU input. Typically MCU inputs are very high impedence and require little to no current at all. I could not find any specification on minimal input current for our MCUs GPIO, but I assume it is ok if we meet the same current requirements that their own internal weak pull-up resistors offer. So we ill go with the maximum value of IPUR of 400µA. I am sure the MCU needs much less. So as long was we can provide 400µA we should be fine. “driving” the MCU really isn't so much the issue as just simply making sure the optoisolator is sufficiently driven by the input LED to turn it on and off.

Given we want an IC > 0.4mA. Figure 3 of the LTV-816 datasheet indicates that if IF is greater than 2mA, VCE is about 0.5V if IC is < 0.5mA.

So for IF > 2mA, VF = 1.2V, using ohms law:

R_F = {V_"IN" - V_F} over I_F ={5.0V - 1.2V} over {.002A} = 3.8V over .002A = 1900 ohms

So as long was we we have no more than a 1900Ω resistor in series with the optoisolator LED, we will have achieved output transistor saturation. However let's just use a nominal RF = 470Ω. We the back calculate to find IF;

I_F = {V_"IN" - V_F} over R_F ={5.0V - 1.2V} over {470 ohm} = 3.8V over 470 ohm = 8.09 mA

which again by Figure 3 in the LTV-816 datasheet is more than enough current to saturate the output transistor. If IF = 8mA, VCE(sat) = 0.5V when IC = 0.5mA

Note: Perhaps a 1-kΩ resistor should be used instead.Something to consider. If anything to just keep the different kinds of parts used to a minimum and would still meet the requirements.

If we use a nominal RF = 1-kΩ. We the back calculate to find IF;

I_F = {V_"IN" - V_F} over R_F ={5.0V - 1.2V} over {1000 ohm} = 3.8V over 1000 ohm = 3.8 mA

which is still above the required forward current of 2mA. A 1-kΩ resistor will be used in the next revision.

So now onto the output stage. Again using ohm's law we see that;

R_C = {V_"IN" - V_"CE(sat)"} over I_C = {5.0V - 0.5V} over {0.5 mA} = 9000 ohms

Again, using a typical value of RC = 10kΩ, we see that;

I_C = {V_"IN" - V_"CE(sat)"} over R_C = {5.0V - 0.5V} over {10000 ohms} = 0.450 mA

This means with a value of RF = 470Ω and RC = 10kΩ. We are able to sufficiently drive the optoisolator in the saturation region and deliver enough signal to the MCU input to trigger it. With the configuration shown in Illustration 10, the input is a simple current limiting resistor (RF) and switch in series with an LED. In this configuration all the switch needs to do is ground the cathode of the LED inside the optoisolator and the LED will turn on. When the LED is turned on, the output transistor will be in saturation and switched on. When the transistor is switched on, this creates a path to ground and will signal the MCU input (signal going low) that the trigger(button) has been pressed. Releasing the switch will cause the LED to turn off (as well the output transistor) causing the input of the MCU to read high (VDD = 5.0V) though the effect of pull-up resistor RC.

### Power Supply Design

The power supply exists for the sole purpose of supplying a regulated voltage level to the microcontroller only. This design does not use a regulated voltage for power output devices such as the lamps or signal bell. Instead raw input voltage is switched directly via the high power output stage to those devices. Thus the power supply design needs to consider the power requirements of the microcontroller and indicators exclusively.

The microcontroller needs a stable 5.0V supply, but can tolerate a supply from 2.0V up to 5.5V (absolute maximum rating is 6.5V).

Considering operation of the unit at 25 ºC, from Figure 11-1 of the microcontroller datasheet we see that at FOSC = 4MHz and VDD = 5.0V, IDD = 650 µA to 1100 µA. In sleep mode, the microcontroller will consume between 0.34 and 0.37 µA at VDD = 5.0V.

Table 10.1 of the datasheet indicates that the Supply Current (IDD) is typically 0.625 mA (1.1 mA maximum) when FOSC = 4MHz and VDD = 5.0V. Power-down current (sleep mode) is 0.35 µA (2.4 µA maximum) at VDD = 5.0V. This looks consistent with the data from Figure 11-1. So assuming worst case for the microcontroller, IDD shall be 2 mA maximum.

However we also have some LEDs we need to drive. Specifically the power indication LED (green) and up to 3 signal indication LEDs (red). Worst case is again that all LEDs are driven at the same time, although this never happens during normal operation.

For the LEDs we have the following specifications from their datasheets;

I_F = {V_"IN" - V_F} over {R_F} , where VIN = 5.0V

LED[^1] | Color | VF(V) | RF(Ώ) | IF(mA)
SSL-LX5093GD (http://www.lumex.com/specs/SSL-LX5093GD.pdf) | Green | 2.2 | 1k | 2.8
SSL-LX5093HD (http://www.lumex.com/specs/SSL-LX5093HD.pdf) | Red | 2 | 1k | 3

With one green and three red LEDs the maximum current consumption is about 11.8 mA for all LEDs. Add this to the microcontroller 2 mA required we arrive at 13.8 mA. No sweat, designing for a reasonable yet well over engineered rating of 100 mA will give us plenty of power supply capacity, especially if we decide to modify or enhance the circuit later.

So the power supply we need to design is a 5.0 V, 100 mA, 1/2 watt power supply. The input voltage is expected to come from a small motorcycle or lawn tractor battery (nominally 12 VDC) but input voltage from a battery can very depending on charge level. Alternatively AC-line maybe used given a step-down transformer and bridge-rectifier is in place (See my Full Wave Rectifier Design (http://www.kevinmfodor.com/home/electronics-projects-1/full-wave-bridge-rectifier)).

A very popular switching voltage converter is the LM2574. The LM2574N-5.0G (http://www.onsemi.com/PowerSolutions/product.do?id=LM2574) is a fixed 5.0 V version which can provide upto 500 mA with an input voltage from 4.75 V to 40 V which costs about $1.62 in single units. This should work perfectly for our application. The datasheet contains an excellent guide to help design the power supply and is illustrated below.

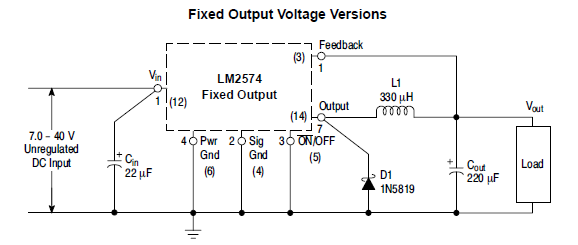
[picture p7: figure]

Illustration 11: Voltage Regulator Reference Circuit

Using the design guide (pg. 10) from the datasheet and given;

VOUT = 5.0 V

VIN(max) = 18 V (typically 13.6 VDC from battery)

ILOAD = 100 mA (over 7x fudge)

We then need to find the values for CIN, D1, L1, and COUT to complete our design.

CIN - To prevent large voltage transients from appearing at the input and for stable operation of the converter, an aluminium or tantalum electrolytic bypass capacitor is needed between the input pin +Vin and ground pin Gnd. This capacitor should be located close to the IC using short leads. This capacitor should have a low ESR (Equivalent Series Resistance) value. A 22 µF, 25 V aluminium electrolytic capacitor located near to the input and ground pins provides sufficient bypassing. I have chosen a Panasonic EEU-FR1H220 (http://www.mouser.com/catalog/specsheets/EEU-FR%20Data%20Sheet.pdf), which is 22 µF, has a low ESR and rated voltage range of 6.3 VDC to 50 VDC.

D1 = Fast recovery catch diode must be rated at > 1.2 x ILOAD = 120 mA, but the datasheet still recommends to use the maximum the IC can handle (500 mA) thus 1.2x that is 600 mA.

Reverse voltage needs to be 1.25x maximum input voltage (22.5V). Therefore we need a 600 mA, 22.5 PIV catch diode. A 1N5817 (http://www.st.com/internet/com/TECHNICAL_RESOURCES/TECHNICAL_LITERATURE/DATASHEET/CD00001625.pdf) low-drop power schottky rectifier easily meets and exceeds this spec. The 1N5817 is very common diode (only $0.12 ea) and has specifications such as IF = 1A, VRRM = 20V and VF = 0.45V. Note the VRRM is very close to 22.5 PIV, but I think we are ok. If in doubt perhaps a 1N5819 could be used instead as it has a VRRM of 30V. The 1N5819 has a VRRM of 40V.

Note: In the next revision the 1N5819 will be used instead of the 1N5817. This will provide a more than adequate VRRM of 40V and is nearly the same cost and exactly the same package as the 1N5817.

L1 = Inductor Selection: Use the inductor selection guide shown in Figure 20 of the datasheet. From the selection guide, the inductance area intersected between the 10 and 20 V lines and 0.1A is mostly represented by 680 indicating a 680µH inductor is required. Current requirements are called out by the equation (at 500 mA). A suitable inductor is the Murata 12LRS684C (http://www.murata-ps.com/data/magnetics/kmp_1200lr.pdf) 680µH, 0.50A maximum DC current inductor.

Note: I used 330µH, 0.63 A part only because it is a very common value and works well over a large output range.Prototype has shown that this value works fine in this application. However I plan to replace this with a 680µH 0.125A inductor in the next revision to more closely match the actual power supply needs.

COUT = Output Capacitor: For stable operation and an acceptable ripple voltage, (approximately 1% of the output voltage) a value between 100µF and 470µF is recommended. Due to the fact that the higher voltage electrolytic capacitors generally have lower ESR (Equivalent Series Resistance) numbers, the output capacitor’s voltage rating should be at least 1.5 times greater than the output voltage. For a 5.0V regulator, a rating at least 8.0V is appropriate, and a 10V or 16V rating is recommended. Therefore the part selected is a Panasonic EEU-FR1H221 (http://www.mouser.com/catalog/specsheets/EEU-FR%20Data%20Sheet.pdf) which is 220 µF, has a low ESR and rated voltage range of 6.3 VDC to 50 VDC.

Note: A lower voltage rated capacitor could be used. A 16V version would be sufficient. The next revision will include a lower voltage capacitor which will also be smaller.

Finally with the power supply designed, we also consider input voltage reverse polarity protection. This feature was added because since this is to be used in the field, conditions may lend themselves to hot swapping a battery mistakenly in the reverse direction. Adding this protection is a simple effort. Battery input reverse voltage can be protected against by insering a 1N5817 (http://www.st.com/internet/com/TECHNICAL_RESOURCES/TECHNICAL_LITERATURE/DATASHEET/CD00001625.pdf) Schottkey Diode in series with the power supply input. Even at worst case expected peak current draw of 0.1A, VF=0.45V thus PD = IF x VF = 0.045 watts. Rth(ja) = 100ºC/W, thus Tj = 4.5ºC + 25ºC(ambient) = 29.5ºC (the part can handle 150ºC max). We will loose about 0.45V off of our input power supply (and dissipate 0.045 watts of power, worst case), but we are providing at least a 12VDC supply anyway. So this should not be an issue.

Note: The next revision will use the 1N5819 (http://www.st.com/internet/com/TECHNICAL_RESOURCES/TECHNICAL_LITERATURE/DATASHEET/CD00001625.pdf) to keep the number of different parts required to a minimum and still meet the (actually exceed) the input reverse voltage protection needs. The 1N5819 (http://www.st.com/internet/com/TECHNICAL_RESOURCES/TECHNICAL_LITERATURE/DATASHEET/CD00001625.pdf) does have a slightly higher forward-voltage drop, VF = 0.6V (resulting in an extra 0.015 watts) but we still have more than enough headroom with a 12V battery supply.

The required output of this power supply is very low (< 20 mA) and therefore power dissipation is very small. For this reason heatsinking was not considered in this design.

## PCB Design

For this design Cadsoft's EAGLE (http://www.cadsoftusa.com/) PCB design software will be used. This was chosen for its popularity and availability for hobbiest, non-commercial designs. It offers convenient schematic capture with integrated PCB layout tools.

As for physical size of the PCB, it would be nice for it to fit inside the 1-1/2” SCH-40 PVC Pipe. The inside diameter is a nominal value 1.610”. However if not possible this ok as when an external power supply is required it is likely to be mounted in an outside water-resistent enclosure anyway.

The PCB shall provide holes to accomodate four #4 phillips button head screws for mounting inside an enclosure or other ridgid surface. PCB material is 2-Sided, FR-4, 1-oz/ft² (35µm) copper board thickness of 1.6mm. These are the most common specifications of 2-sided PCB board house manufacturers.

All components will be through-hole parts to fascilitate simple assembly and moderate soldering skills.

Working grid is 50 mils, with 10 mils routing to grid. Basic single tracks (width/spacing, mils) are;

- 10/10 signals
- 20/20 for VCC and GND,
- 40/40 for Battery (assumes ~2.4 Amps)

Trace minimum width guidelines for 1-oz/ft² (35µm) copper, 10 ºC rise;

2A, Twidth = 31.3mil

3A, Twidth = 55.0 mil

4A, Twidth = 82.7 mil

Ground and Power Plan Pour is 0.012 mil width, 0.012 mil isolate with thermals and orphans.

Larger tracks will be used whereever possible.

## Software Design

Like most control systems, their implmentation lends itself well to a finite state machine (FSM). If implemented properly they are easy to understand and maintain.

TODO: Main-loop, Input Debounce, Signal FSM

## Retrospect

In the process of developing, building and testing the Rev.A version of the GCSC-II board, some further improvements on some of the initial design choices were identified. Like any design there always seems to be room for further improvements, and this is no exception. To address these further design changes I have compiled the list below;

Summary of Notes for Revision A

- Inductor L1 should be replaced with a 680µH, 0.125A inductor (Bourns RLB0608-681KL (http://www.bourns.com/data/global/pdfs/rlb.pdf)) which has the same footprint as the Rev.A inductor. Since the current requirements of the power supply are low enough (well below 100 mA) this is a more suitable inductor.
- Remove the 100-kΩ bleeder resistors R5, R7 and R9. They are not needed in this design as the input to the MOSFET gates are never left floating. Since the gate is always driven or held off, these resistors are not necessary. Removing them will reduce part count, layout complexity and area as well as reduce cost.
- Instead of the 1N4007 (http://www.fairchildsemi.com/ds/1N/1N4001.pdf) freewheel/clamping diode (D3), consider using a 1N5819 (http://www.fairchildsemi.com/ds/1N/1N5819.pdf) fast-acting diode which also comes in a DO-41 package. The 1N5819 (http://www.fairchildsemi.com/ds/1N/1N5819.pdf) features a maximum PD = 1.25 W, IFSM = 25A, andVF of 0.6V. The maximum voltage rate of change for this device is, dV/dt = 10kV/µs superior to the 1N4007 (http://www.fairchildsemi.com/ds/1N/1N4001.pdf).
- Instead of the 1N5817 (http://www.fairchildsemi.com/ds/1N/1N5819.pdf) power supply flyback diode (D2), consider a 1N5819 (http://www.fairchildsemi.com/ds/1N/1N5819.pdf) which has higher VRRM rating of 40V in the same DO-41 package which exceeds the needed specification for this power supply output.
- Instead of the 1N5817 (http://www.fairchildsemi.com/ds/1N/1N5819.pdf) diode (D1) as reverse input voltage protection, use the 1N5819 (http://www.fairchildsemi.com/ds/1N/1N5819.pdf) since the specs are better (VRRM of 40V vs. 20V), but more importantly to reduce the number of different parts needed. Since the 1N5819 (http://www.fairchildsemi.com/ds/1N/1N5819.pdf) will be used in other areas as well this reduces the number of unique parts required and is available in the same DO-41 package. The 1N5819 (http://www.fairchildsemi.com/ds/1N/1N5819.pdf) has a slightly higher forward-voltage drop, VF = 0.6V (opposed to the 1N5817 (http://www.fairchildsemi.com/ds/1N/1N5819.pdf)'s VF = 0.45V) but it is still more than adequate for the job.
- Use a 1-kΩ resistor (R3, trigger input) instead of the 470-Ω resistor. This choice will still deliver the required > 2mA of current (3.8mA in this case) and if anything else will keep the different kinds of parts used to a minimum since this same value is used for R1, R4, R6, and R8.
- Use a lower voltage capacitor rating for C2. This would also be a smaller footprint. The Panasonic EEU-FR1C221 (http://www.mouser.com/catalog/specsheets/EEU-FR%20Data%20Sheet.pdf) is a better choice and sufficient to meet spec with a voltage rating of 16V.
- PCB footprint for LED1-4 could be changed to the 3mm version (T-1) such as the Lumex SSL-LX3044HD (http://www.lumex.com/specs/SSL-LX3044HD.pdf) (RED) and Lumex SSL-LX3044GD (http://www.lumex.com/specs/SSL-LX3044GD.pdf) GREEN devices which have the same operating specs, but are available in a smaller footprint package.
- Remove JP2 (external trigger) it doesn't really seem needed, but instead use a jumper (2-pin) footprint just in case someone wants to solder one in.
- J1 and JP1 should be larger connectors with perhaps a wider pitch and able to accept the 18 AWG wire more easily with crimp-type terminals (the terminals and matching connectors in Error: Reference source not found page Error: Reference source not found are a bit tight). Instead use Molex KK-style 0.156” pitch connectors which can handle 18 AWG wireis preferred. Please refer to the Molex Web Catalog (http://www.molex.com/catalog/web_catalog/pdfs/D.pdf) page 2. The Molex Series #2478 crimp (http://www.molex.com/webdocs/datasheets/pdf/en-us/0008500116_CRIMP_TERMINALS.pdf)terminal (http://www.molex.com/webdocs/datasheets/pdf/en-us/0008500116_CRIMP_TERMINALS.pdf), #41792 (http://www.molex.com/molex/products/listview.jsp?query=41792&path=cHome) header and #41695 (http://www.molex.com/molex/products/listview.jsp?query=41695&path=cHome) housing looks like a good choice. There should be two separate connectors (2-pin power, 8-pin mast) placed in-line on the same edge of the PCB.
- PicKit3 doesn't work in circuit when LAMP2 MOSFET(Q2), on GP1 is inserted. This is due to the fact that GP0, GP1 and GP3 must be isolated from the application circuit for the ICSP mode to work properly. A small isolation pad or jumper could be inserted to allow these pins to be isolated easily. GP3 is already sufficiently isolated since when the trigger is not pressed only a pull-up resistor (R2) is connected to to the pin. Trace lengths should be kept to a minimum.
- PCB routing/traces should have more consideration for Power Supply layout (see the datasheet) and output connector. Minimum 2A traces with grounds going back to the supply. Separate MCU and Power grounds would be better as well and provide better isolation from power dips/surges when high-power loads such as the bell and lamps are actuated.
- PCB layout for MOSFETs should use free standing footprint versions rather than those which lay down flat. Would result in less board space and perhaps simpler routing. Maximum power dissipation, PD = 53 mW and junction temperature TӨj = 30.77 ºC (87.39 ºF), which is 6 ºC (or 11 ºF above ambient) are well below the MOSFETs maximum ratings of, PD(max) = 1.38 W and TӨj(max) = 175 ºC. No heatsinking from the underlying PCB pad is needed.
- Since component count will be less and footprints will be smaller, consider keeping size of board to under 5cm x 5cm which is iTead maximum size for their least expensive production run.

[^1] The next revision will replace the 5mm LEDs (T-1 ¾) with a 3mm LED (T-1) that possesses the same operating characteristics.

2 of 30 Kevin Fodor

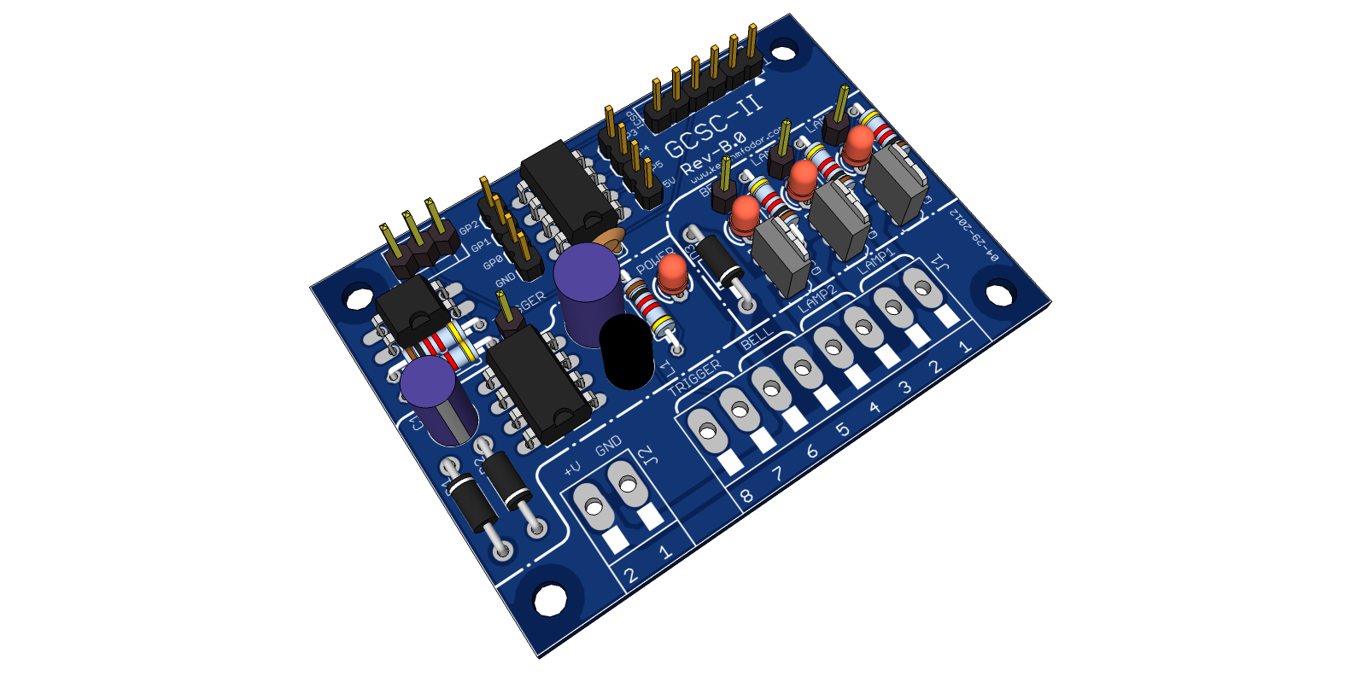
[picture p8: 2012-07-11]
images/gcsc-ii.png

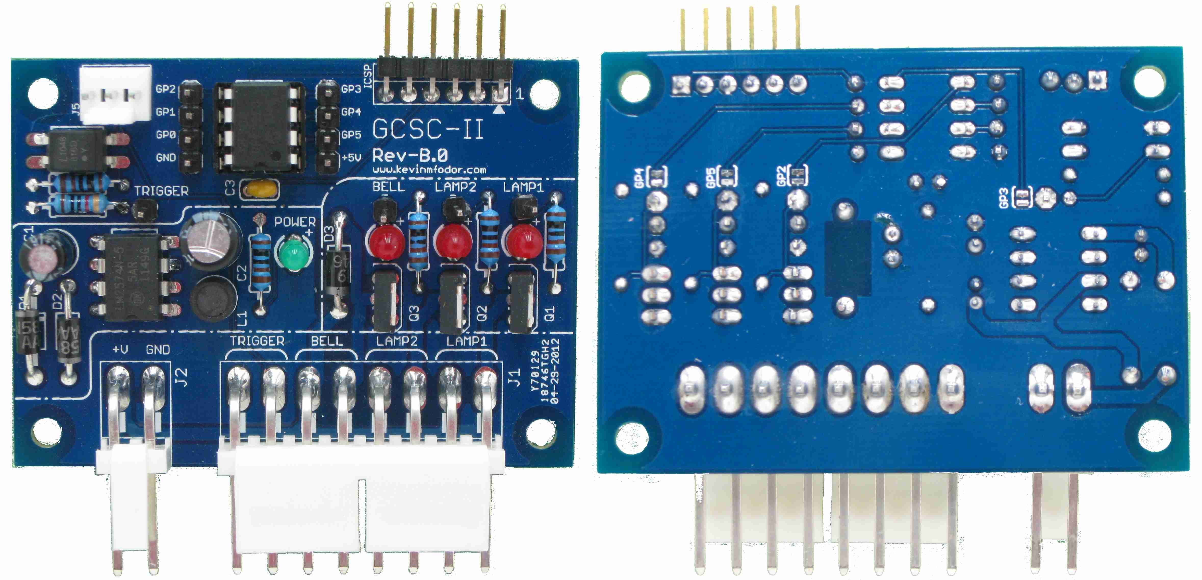
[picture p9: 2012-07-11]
images/wiki/gcsc-ii_pcb_both_isolated.jpg

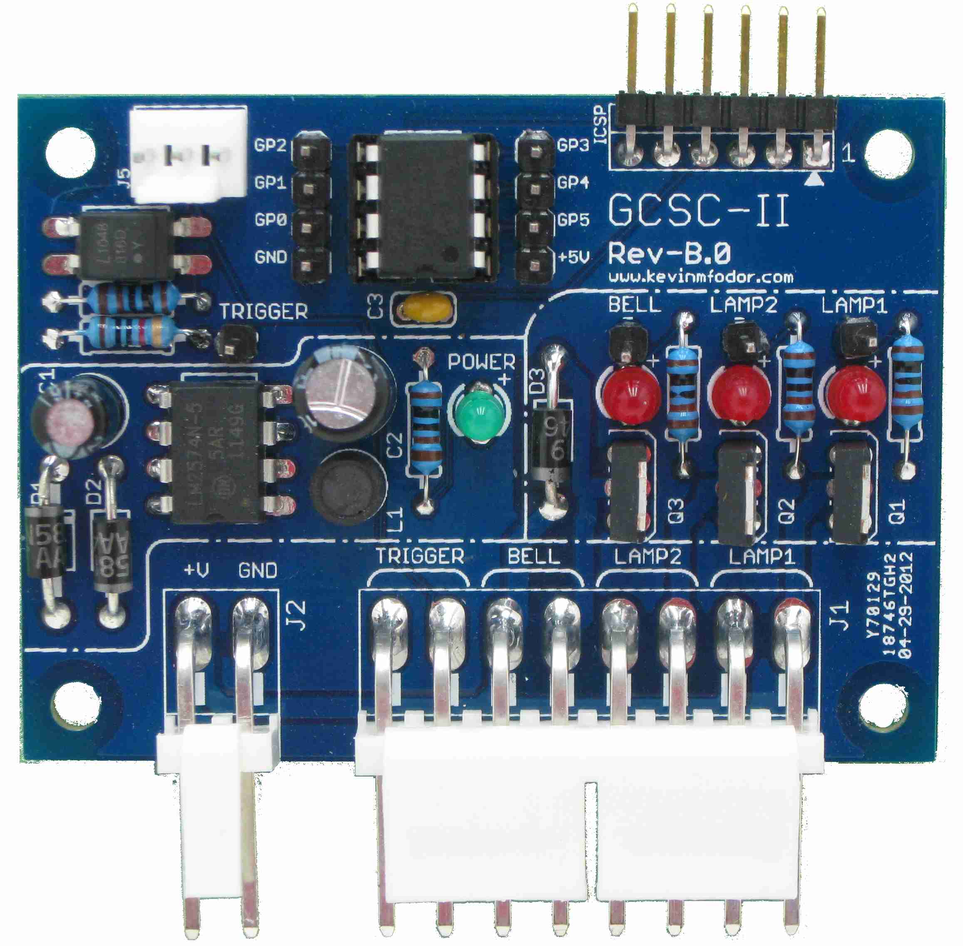
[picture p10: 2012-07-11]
images/wiki/gcsc-ii_pcb_front_isolated.jpg

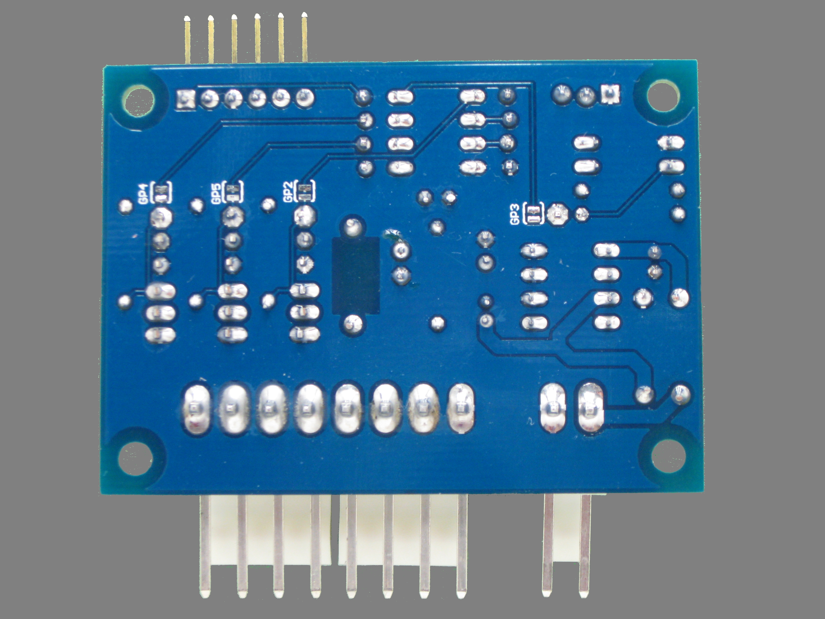
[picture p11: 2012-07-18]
images/wiki/gcsc-ii_pcb_back_grey.jpg

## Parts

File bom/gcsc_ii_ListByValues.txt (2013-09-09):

Qty	Value	Part Num	Package	Parts	Mfg Name	VID	Vendor Part Num	Description	Customer Ref	XREF
1	0.1uF	21RZ310-RC	C025-024X044	C3	Xicon	ME	21RZ310-RC	Multilayer Ceramic Capacitors (MLCC) - Leaded .1uF 50volts Z5U 20% 2.5mm L/S	*	REF6
3	1N5819	1N5819	DO41-10	D1, D2, D3	Fairchild Semiconductor	ME	512-1N5819	Schottky (Diodes & Rectifiers) Schottky Barrier	*	REF17
5	1k	299-1K-RC	0207/10	R1, R3, R4, R5, R6	Xicon	ME	299-1K-RC	Carbon Film Resistors - Through Hole 1.0Kohms 0.05	*	REF9
1	10k	299-10K-RC	0207/10	R2	Xicon	ME	299-10K-RC	Carbon Film Resistors - Through Hole 10Kohms 5%	*	REF8
1	22uF	EEU-FR1H220	E2-5	C1	Panasonic	ME	667-EEU-FR1H220	Aluminum Electrolytic Capacitors - Leaded 50VDC 22uF 5x11mm LS2mm	*	REF13
1	220uF	EEU-FR1C221	E2,5-6,3	C2	Panasonic	ME	667-EEU-FR1C221	Aluminum Electrolytic Capacitors - Leaded 16VDC 220uF 6.3x11.2mm LS2.5mm	*	REF7
1	680uH	RLB0608-681KL	RLB0608	L1	Bourns	ME	652-RLB0608-681KL	Power Inductors 680uH 10% 125mA	*	REF16
1	EXT	22-27-2031	MOLEX-1X3_LOCK	J5	Molex	ME	538-22-27-2031	Headers & Wire Housings 3C STR HEADER W/FRLK	*	REF22
1	LM2574N-2-5.0	LM2574N-5G	DIL8	IC1	On Semiconductor	ME	863-LM2574N-5G	Switching Converters, Regulators & Controllers 5V .5A PWR SW REG	*	REF10
1	LTV-816	LTV-816	DIL04	IC2	Lite-On	ME	859-LTV-816	Transistor Output Optocouplers Optocoupler Phototrans	*	REF12
1	MAST	26-60-5080	KK-156-8-RA	J1	Molex	ME	538-26-60-5080	Headers & Wire Housings R/A PCB HDR 8P TIN FRICTION LOCK	*	REF19
3	NTD4906N-35G	NTD4906N-35G	I-PAK_STRAIGHT_LEAD	Q1, Q2, Q3	On Semiconductor	ME	863-NTD4906N-35G	MOSFET NFET DPAK 30V 54A 5.5 mOhm	*	REF4
1	PIC12C508JN	PIC12F508-I/P	DIL8	IC3	Microchip	ME	579-PIC12F508-I/P	Microcontrollers (MCU) 1 KB 25 RAM 6 I/O Ind Temp PDIP8	*	REF11
1	POWER	26-60-5020	KK-156-2-RA	J2	Molex	ME	538-26-60-5020	Headers & Wire Housings R/A PCB HDR 2P TIN FRICTION LOCK	*	REF18
1	SSL-LX3044GD	SSL-LX3044GD	LED3MM	LED1	Lumex	ME	696-SSL-LX3044GD	Standard LED - Through Hole 3mm Short Lens Green	*	REF15
3	SSL-LX3044HD	SSL-LX3044HD	LED3MM	LED2, LED3, LED4	Lumex	ME	696-SSL-LX3044HD	Standard LED - Through Hole 3mm Short Lens Red	*	REF14

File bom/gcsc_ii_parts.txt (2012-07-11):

Partlist

Exported from gcsc_ii.sch at 5/1/2012 7:53:26 AM

EAGLE Version 6.2.0 Copyright (c) 1988-2012 CadSoft

Assembly variant: 

Part       Value          Device             Package             Library  Sheet

BELL.OUT   BELL           LSP10              LSP10               kevin    1
C1         22uF           CPOL-USFR-5        E2-5                kevin    1
C2         220uF          CPOL-USFR-6,3      E2,5-6,3            kevin    1
C3         0.1uF          C-USC025-024X044   C025-024X044        kevin    1
D1         1N5819         SCHOTTKY-DIODEDO41 DO41-10             kevin    1
D2         1N5819         SCHOTTKY-DIODEDO41 DO41-10             kevin    1
D3         1N5819         SCHOTTKY-DIODEDO41 DO41-10             kevin    1
GP2        GP2            SJ_CLOSED          SJ_2S-TRACE         kevin    1
GP3        GP3            SJ_CLOSED          SJ_2S-TRACE         kevin    1
GP4        GP4            SJ_CLOSED          SJ_2S-TRACE         kevin    1
GP5        GP5            SJ_CLOSED          SJ_2S-TRACE         kevin    1
IC1        LM2574N-2-5.0  LM2574N-2-5.0      DIL8                kevin    1
IC2        LTV-816        LTV816             DIL04               kevin    1
IC3        PIC12C508JN    PIC12C508JN        DIL8                kevin    1
ICSP       PIC_ICSP_RA    PIC_ICSP_RA        PIC_ICSP            kevin    1
J1         MAST           KK-156-8-RA        KK-156-8-RA         kevin    1
J2         POWER          KK-156-2RA         KK-156-2-RA         kevin    1
J3         IC3_1-4        M04LOCK            1X04_LOCK           kevin    1
J4         IC3_5-8        M04LOCK            1X04_LOCK           kevin    1
J5         EXT            M03POLAR_LOCK      MOLEX-1X3_LOCK      kevin    1
L1         680uH          RLB0608            RLB0608             kevin    1
LAMP1.OUT  LAMP1          LSP10              LSP10               kevin    1
LAMP2.OUT  LAMP2          LSP10              LSP10               kevin    1
LED1       SSL-LX3044GD   LED3MM             LED3MM              kevin    1
LED2       SSL-LX3044HD   LED3MM             LED3MM              kevin    1
LED3       SSL-LX3044HD   LED3MM             LED3MM              kevin    1
LED4       SSL-LX3044HD   LED3MM             LED3MM              kevin    1
Q1         NTD4906N-35G   NTD4906N           I-PAK_STRAIGHT_LEAD kevin    1
Q2         NTD4906N-35G   NTD4906N           I-PAK_STRAIGHT_LEAD kevin    1
Q3         NTD4906N-35G   NTD4906N           I-PAK_STRAIGHT_LEAD kevin    1
R1         1k             R-US0207/10        0207/10             kevin    1
R2         10k            R-US0207/10        0207/10             kevin    1
R3         1k             R-US0207/10        0207/10             kevin    1
R4         1k             R-US0207/10        0207/10             kevin    1
R5         1k             R-US0207/10        0207/10             kevin    1
R6         1k             R-US0207/10        0207/10             kevin    1
TRIGGER.IN TRIGGER        LSP10              LSP10               kevin    1

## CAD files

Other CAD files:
sketchup/gcsc-ii.skp

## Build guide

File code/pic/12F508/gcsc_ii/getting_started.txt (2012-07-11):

This project is a general template file for the PIC12 Family of
microcontrollers.  It's purpose is to provide a project shell for users to
get started designing their own applications.  Final qualification and testing
of this project is left to the user.

ADVANCED USER TIP

From the main menu, refer to the Task list by going to Window > Tasks (Ctrl+6).
As long as the task window is not configured to filter out any tasks,
the getting started TODO list embedded in this project will be displayed.

Make sure the 'Show tasks for the main project and for the open projects which
depend on it' option is selected on the left hand side of the Tasks window so
that tasks related to other projects are not active.

HOW TO ADD YOUR OWN CODE TO A TEMPLATE

STEP 1

First install the appropriate C compiler if you have not done so already.

See www.microchip.com/compilers

Next, build this project by clicking the Clean and Build Icon (the hammer and
broom symbol) in the MPLAB X IDE Toolbar.  If this project builds, then you are
ready to make changes for your own application.  If the project does not build,
you need to troubleshoot why the project does not build before moving on.

STEP 2

Embed your device's configuration bits into the code.  Instructions for this
are commented in configuration_bits.c

STEP 3

Unless interrupts are not used in your application, fill in the interrupt
vector code.  Code stubs are provided in interrupts.c.  Check the device
datasheet to confirm that you are servicing all the relevant enabled
interrupts in your application within the ISR.  Note that it is important
to check interrupt flags in sequence within one conditional statement to
avoid interrupt contention which could result in corrupting the interrupt
context.

STEP 4

Define system parameters such as the system operating frequency in system.h.

If your device stores an oscillator calibration value at the end of program
memory, incorporate the _READ_OSCCAL_DATA() function in system.c.  The device
datasheet will tell you if calibration data is stored at the end of the
device memory.

Add system level functions to system.h and system.c.  For example, if
you want a function to determine the reset source of the device to know if you
need to backup data, do an oscillator switch, enter a low power mode, etc...
these types of functions may be added to system.c and prototypes can go in
system.h.

STEP 5

Add user level functions to user.h and user.c.  User level functions are
functions that initialize I/O, initialize user peripherals like the ADC,
compute user algorithms, perform calculations on sampled user data, and so on.
User function prototypes and macros may be placed in user.h, and user
functions themselves may go in user.c

STEP 6

Add code to main.c on the line that says <INSERT USER APPLICATION CODE HERE>.
For example, here you would call functions in user.c or system.c, or possibly
setup your own state machine or primary code loop.

Global variables may be added to main.c as well.  As a general practice, macros
and prototypes may go in header files, but variable declarations should not
go in .h files.  Variable declarations should be placed in .c files.

STEP 7

Design the rest of your application.  Add new files to the application, and
test the finished product.

STEP 8

Document what the project does and include other project information in
project_information.txt.

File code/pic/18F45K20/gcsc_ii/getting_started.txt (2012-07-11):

This project is a general template file for the PIC18 Family of
microcontrollers.  It's purpose is to provide a project shell for users to
get started designing their own applications.  Final qualification and testing
of this project is left to the user.

ADVANCED USER TIP

From the main menu, refer to the Task list by going to Window > Tasks (Ctrl+6).
As long as the task window is not configured to filter out any tasks,
the getting started TODO list embedded in this project will be displayed.

Make sure the 'Show tasks for the main project and for the open projects which
depend on it' option is selected on the left hand side of the Tasks window so
that tasks related to other projects are not active.

HOW TO ADD YOUR OWN CODE TO A TEMPLATE

STEP 1

First install the appropriate C compiler if you have not done so already.

See www.microchip.com/compilers

Next, build this project by clicking the Clean and Build Icon (the hammer and
broom symbol) in the MPLAB X IDE Toolbar.  If this project builds, then you are
ready to make changes for your own application.  If the project does not build,
you need to troubleshoot why the project does not build before moving on.

STEP 2

Embed your device's configuration bits into the code.  Instructions for this
are commented in configuration_bits.c

STEP 3

Unless interrupts are not used in your application, fill in the interrupt
vector code.  Code stubs are provided in interrupts.c.  Check the device
datasheet to confirm that you are servicing all the relevant enabled
interrupts in your application within the ISR.  Note that it is important
to check interrupt flags in sequence within one conditional statement to
avoid interrupt contention which could result in corrupting the interrupt
context.

STEP 4

Define system parameters such as the system operating frequency in system.h.

Add system level functions to system.h and system.c.  For example, if
you want a function to determine the reset source of the device to know if you
need to backup data, do an oscillator switch, enter a low power mode, etc...
these types of functions may be added to system.c and prototypes can go in
system.h.

STEP 5

Add user level functions to user.h and user.c.  User level functions are
functions that initialize I/O, initialize user peripherals like the ADC,
compute user algorithms, perform calculations on sampled user data, and so on.
User function prototypes and macros may be placed in user.h, and user
functions themselves may go in user.c

STEP 6

Add code to main.c on the line that says <INSERT USER APPLICATION CODE HERE>.
For example, here you would call functions in user.c or system.c, or possibly
setup your own state machine or primary code loop.

Global variables may be added to main.c as well.  As a general practice, macros
and prototypes may go in header files, but variable declarations should not 
go in .h files.  Variable declarations should be placed in .c files.

STEP 7

Design the rest of your application.  Add new files to the application, and
test the finished product.

STEP 8

Document what the project does and include other project information in
project_information.txt.

KNOWN ISSUE:

The native build output for this project may include this message:

"The Extended CPU Mode configuration bit is enabled, but the program was not
built using extended CPU instructions.  Therefore, your code may not work
properly."

The reason for this is that although configuration_bits.c includes
instructions for including configuration macros, they are not actually included
and by default the Extended CPU Mode is enabled.  As soon as the macros are
embedded with the Extended CPU Mode off, or extended CPU mode is enabled in the
build, then this message will go away.

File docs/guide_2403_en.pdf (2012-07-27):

# Railroad Grade Crossing Signal Controller

Author: Kevin Fodor

Tools used in this project PanaVise (http://makeprojects.com/Item/PanaVise) (1)
Solder (http://makeprojects.com/Item/Solder) (1)
Soldering iron (http://makeprojects.com/Item/Soldering_iron) (1)
Wire cutter/stripper (http://makeprojects.com/Item/Wire_cutter_stripper) (1)

Parts relevant to this project GCSC-II Blank PCB (http://makeprojects.com/Item/GCSC-II_Blank_PCB) (1)
GCSC-II Components Pack (http://makeprojects.com/Item/GCSC-II_Components_Pack) (1) 8-Pin IC Socket (http://makeprojects.com/Item/8-Pin_IC_Socket) (2) Optional
9 Volt alkaline battery (http://makeprojects.com/Item/9_Volt_alkaline_battery) (1)
9v battery snap (http://makeprojects.com/Item/9v_battery_snap) (1)
Molex 3.96mm Pitch KK® Crimp Terminal Housing, Friction Ramp, 2 Circuits (http://makeprojects.com/Item/Molex_3.96mm_Pitch_KK%C2%AE_Crimp_Terminal_Housing_Friction_Ramp_2_Circuits) (1) Jumper Wire (http://makeprojects.com/Item/Jumper_Wire) (1) Optional

This project guide explains how to build an operating railroad grade crossing signal controller (GCSC) for controlling a simulated railroad crossing signal that has working flashing lamps and striking bell. Just like the real thing!
This board was also designed with hacking in mind. Due to the on-board 5 VDC power supply and extensive breakout headers and detailed silkscreening it also makes an excellent Microchip PIC12 development board. The I/O pins used for the GCSC-II implementation can be detached though small cut-trace pads on the back of the board so that you can route the micro's I/O pins to anywhere you like. Separately the opto-isolated input and 3 high-power outputs can be re-purposed for many other projects and experiments. You can even try connecting them to your own bread board for off-board development. All of the design and documentation for this project is maintained on a GoogleCode project site which you can find at this link: http://code.google.com/p/gcsc-ii/
There you will find the gerbers, (http://code.google.com/p/gcsc-ii/downloads/detail?name=gcsc-ii_rev-b-0_gerbers.zip) complete parts lists (http://code.google.com/p/gcsc-ii/source/browse/bom/gcsc_ii_parts.txt) and detailed design documentation for this board. Also feel free to contribute further on that site.
Along with my Blog post, (http://www.kevinmfodor.com/home/My-Blog/operatingrailroadsignalcrossing-ii) this video (http://youtu.be/4bryCb7wb8Q) shows one example of what can be done with this controller.
I hope you enjoy building and hacking this board as much as I did designing it. If you have done something with it and found it helpful, drop me a line. I would love to hear about it.

### Railroad Grade Crossing Signal Controller

© Make Projects | www.makeprojects.com | Page 1 of 10

Step 1 — Get familiar with the blank PCB

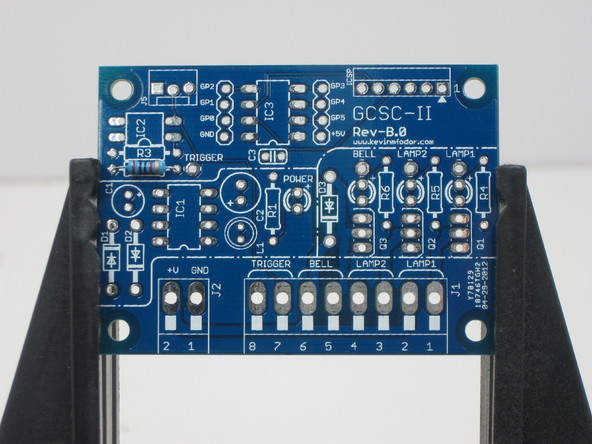
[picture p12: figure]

Step 2 — Place 10k resistor

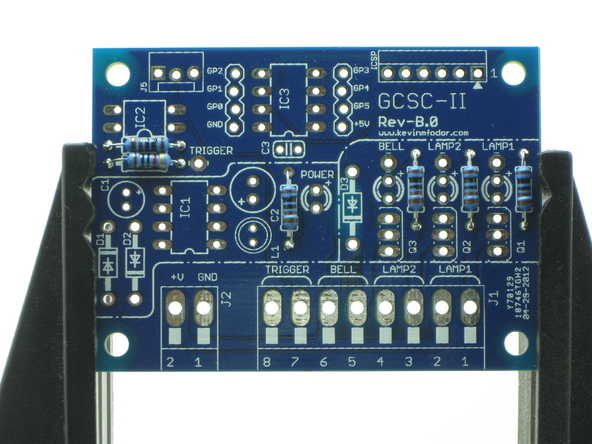
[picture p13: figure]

Step 3 — Place five 1k resistors

This is a double-sided through-hole PCB with full silkscreen detail of all parts, placement and sub-system identification.
We will proceed with the smallest profile components first and work our way up to the larger components. Doing it this way allows us to get easy access to all the components while soldering them to the board. Chuck up your PCB into a suitable vise and we can get started.

Bend the leads of the 10k resistor and insert it into the PCB location marked R2 and solder in place. Polarity is not important.

Bend the leads of five1k resistors and insert them into the PCB locations marked R3, R1, R6, R5, R4 and solder in place.
Again, polarity is not important.

Step 4 — Place one 0.1uF capactior

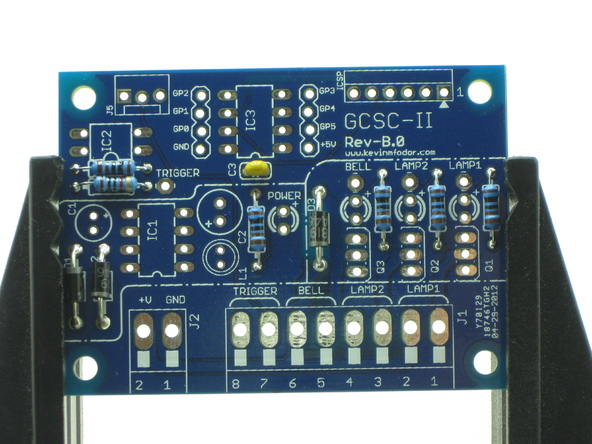
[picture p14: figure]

Step 5 — Place three 1N5819 diodes

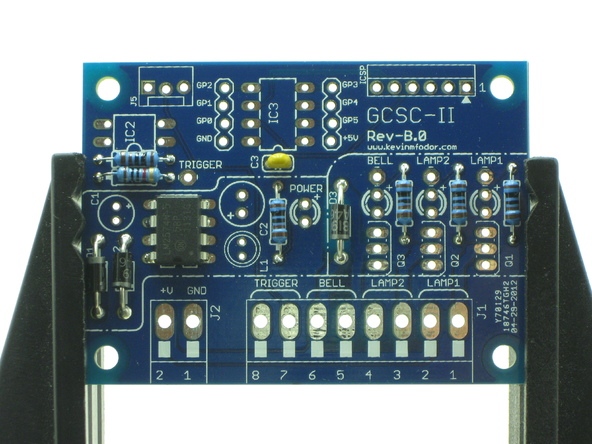
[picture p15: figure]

Step 6 — Place the LM2574 voltage regulator

Place one 0.1uF capactior into the PCB location marked C3. This is the PIC12 microcontroller decoupling capacitor and solder in place.
Note this is a ceramic capacitor without polarity so any direction is fine.

Bend the leads of three 1N5819 diodes and insert them into the PCB locations marked D1, D2, and D3 and solder in place.
Be sure to observe proper orientation by making sure the line and point on the diode is the same orientation as on the PCB. D1 should be up, D2 should be down and D3 should be down as well.

Place the LM2574 voltage regulator (8-pin DIP) into the PCB location IC1 and solder in place.
Be sure to observe proper orientation as the notice (pin 1) needs to be pointing down and aligned as marked on the silkscreen.
Note: You may also choose to used an 8-pin DIP socket instead at this point and replace the chip later. For instance you may want to use a 3.3V version of the regulator instead.

Step 7 — Place the 680uH inductor

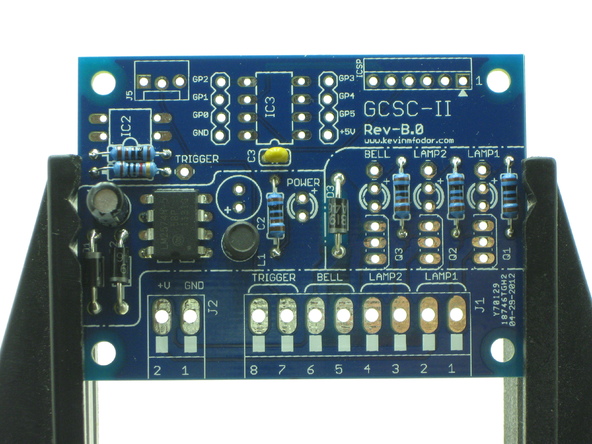
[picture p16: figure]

Step 8 — Place one 22uF electrolytic capacitor

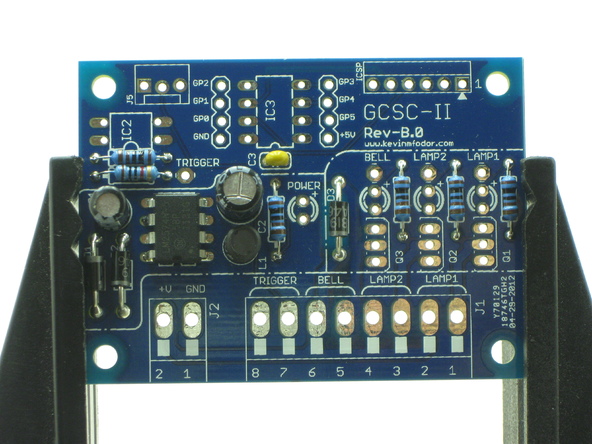
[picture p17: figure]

Step 9 — Place one 220 uF electrolytic capacitor

Place one 680uH inductor into PCB location L1 and solder in place.
Note this is a simple inductor without polarity so any direction is fine.

Place one 22uF electrolytic capacitor into PCB location C1 and solder in place.
Be sure to observe proper polarity by lining up the lead marked "-" with the right hole (the one without the "+").

Place one 220 uF electrolytic capacitor into PCB location C2 and solder in place.
Be sure to observe proper polarity by lining up the lead marked "-" with the right hole (the one without the "+").

Step 10 — Place one 3mm green LED

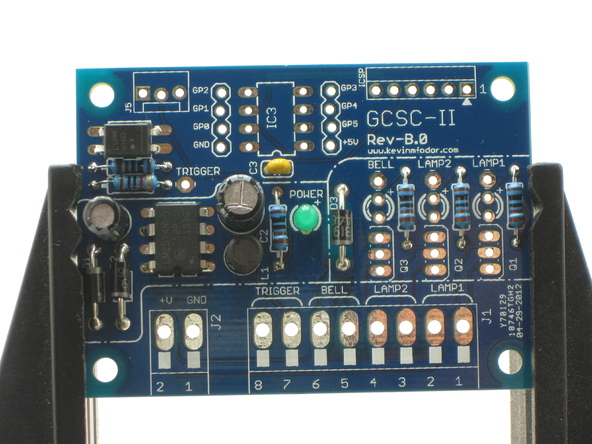
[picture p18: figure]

Step 11 — Place the optoisolator

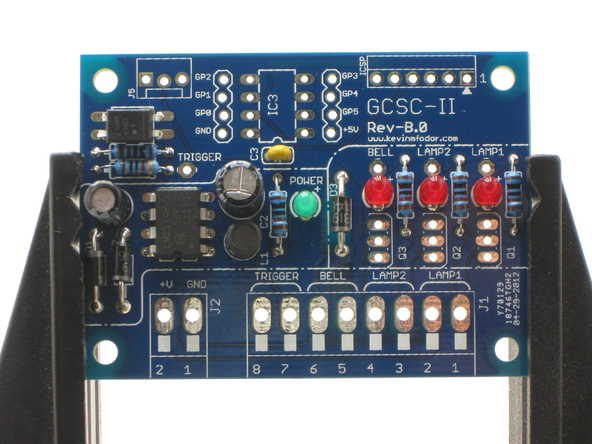
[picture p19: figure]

Step 12 — Place three 3mm red LEDs

Place one 3mm green LED into location POWER and solder in place.
Observe proper polarity. The long lead (ANODE) should go into the hole marked with a "+"

Place the optoisolator into location IC2 and solder in place.
Again, be sure to observe proper orientation as the "dot" (pin 1) must be in alignment with what is on the PCB silkscreen. It should be pointing down next to the resistor R3.

Place three 3mm red LEDs into locations LED2, LED3 and LED4 and solder in place.
Note these are not marked on the silkscreen but they align next to the row of 1k resistors next to Q3, Q2 and Q1.
Observe proper polarity. The long lead (ANODE) should go into the hole marked with a "+"

Step 13 — Insert three power MOSFETs

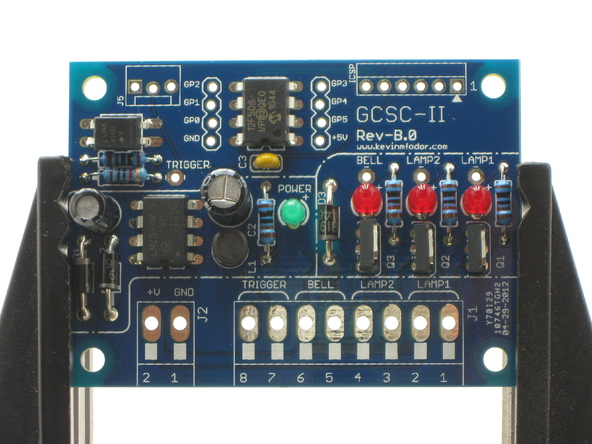
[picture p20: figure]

Step 14 — Insert the PIC12F508 microcontroller

Insert three power MOSFETs into locations Q1, Q2 and Q3 and solder in place.
These are static sensitive devices, use ESD caution.
Be careful to observe proper orientation with these devices. The metal tab should be facing to the right as on the PCB silkscreen.

Insert the PIC12F508 microcontroller into location IC3 and solder in place.
Be sure to observe proper orientation. Notice pin 1 needs to be pointing down and aligned as marked on the silkscreen.
Note: You may decide to solder in an 8-pin DIP socket to accept the microcontroller. DIP sockets allow the easy removeal of an IC from the PCB without desoldering. This is typically done during prototyping and expirimentation. You can reprogram the microcontroller in circuit using the ICSP header, but depending on how abusive your expirimentation is you may want to replace it from time to time. Also at this time you may also want to insert the optional small 3-pin molex connector at location J5. The external connector brings out the regulated +5VDC from the power supply, a ground signal and the trigger input signal. This header is handy for instance if you want the controller to be triggered say be a remote control as described in this project: Got Wireless? Modify a Simple 12VDC Wireless Remote Control for 5VDC Operation

Step 15 — Insert the 8-pin and 2-pin male Molex connectors
Insert the 8-pin and 2-pin male Molex connectors into locations J1 and J2 respectively and solder in place. Secure these connectors in place with small clamps. Align the connectors so they are straight and flush with the PCB.
Start by soldering one pin at each end first, just to tack it into place. Then when satisifed solder the other pins.
Go back and re-flow your solder joints, adding extra solder as needed.
At this point the controller is complete, although you may want to continue to the next step to add optional breakout headers and connectors which make this board even more useful.

Step 16 — Optional - Insert the break-out headers.
The preceeding steps will get you to the point of a fully operational board, but you may want to consider some extra break-out headers to fascilitate hacking this board. If not you can also skip this step.
These 0.10" pitch headers are handy to have if you plan on hacking this board. They bring out all of microcontroller pins, input and output connections to peripherals as well as provide a 6-pin ICSP in-circuit programming port.
Insert the right-angle 0.10" pitch header into the ICSP header location. Optional for operation of the circuit, but is required to program the microcontroller in-circuit. I recommend including it as it is quite helpful to making quick code changes and trying them out.
Insert four straight single 0.10" header pins into the PCB to fascilitate hacking. Place these pins into the connection points for the input signals (trigger) and output signals (lamps and bell). These can also be helpful when hacking this board to do other things. The second photo shows the locations of the cut-trace disconnects which allow you to disconnect the peripherals from the microcontroller's I/O pins. Using the breakout headers these devices can be reconnected to any other pin.
Finally install the pair of 4-pin 0.10" pitch headers for the microcontroller. These header pins are breakout pins which provide access to all 8 microcontroller pins.

Step 17 — Inspect your work

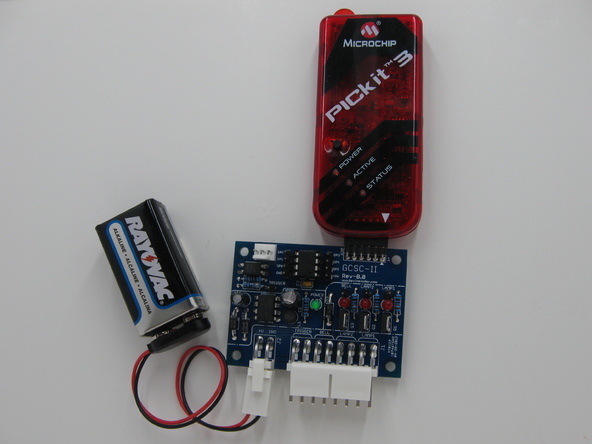
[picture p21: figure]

Step 18 — Program the Microcontroller

Take a look at the completed board.
Do all solder connections look smooth and shiny? Are there any cold-solder joints?
Did any through-hole part leads not get soldered? Are all components snuggly soldered to the board, allowing little movement?
Does it look basically like the completed photo?

If you are not able to obtain a pre-programmed part, you will need to program your microcontroller at least at first with the provided code so you can test it. For this you will need to use a PIC3Kit Programmer / Debugger and the MPLAB X IDE available from (http://www.microchip.com/stellent/idcplg?IdcService=SS_GET_PAGE&nodeId=1406&dDocName=en538340) Microchip. (http://www.microchip.com/)
If you do not have a programmer but need a
device programmed, contact me via this
site and I'll try to help you out.

Step 19 — Test
Step 20 — Use

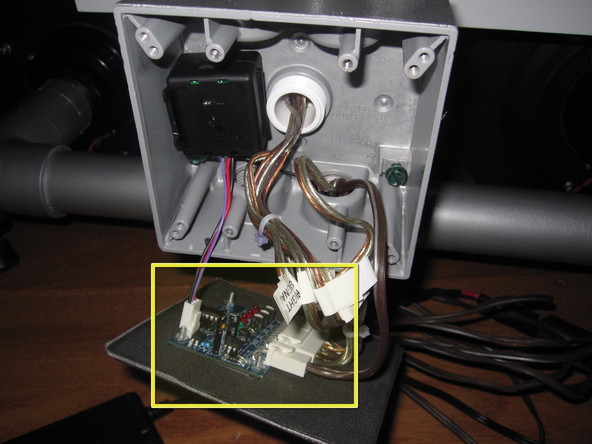
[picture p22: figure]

The embedded controller described here is intended to primarily be used as a controller for a railroad signal crossing. However, because of the addition of breakout headers, an ICSP connector and on-board step-down voltage regulator, it can also be used as a flexible development platform that can accommodate any compatible Microchip 8-pin PIC microcontrollers. This makes this board an excellent launching point for many other projects as well.

This document was last generated on Jul 26, 2012.

To test the controller, it is easiest to connect a 9V battery (or similar) to the power connector J1. The PCB is reverse power polarity protected, but be careful.
Note: a 9V battery is sufficient for running
the controller like this. Since we are not
driving any large loads via the MOSFETs (lamps, etc) 9V battery has plenty of power to run just the controller.
Connect the battery to the power terminals
Trigger the system by touching the TRIGGER pin to GROUND.
The LEDs should begin to flash. The LAMP LEDs should flash approximately every 2/3 seconds while the BELL LED will pulse every 2/3 seconds.
You can short the trigger again and the system should shutoff.
click here for a video of a working controller demonstration: Controller Testing Video (http://youtu.be/66ZCW0Ukxu0)

Now your ready to use your controller either as intended (A Railroad Grade Crossing Signal Controller) or as a PIC12 development kit for your own projects.

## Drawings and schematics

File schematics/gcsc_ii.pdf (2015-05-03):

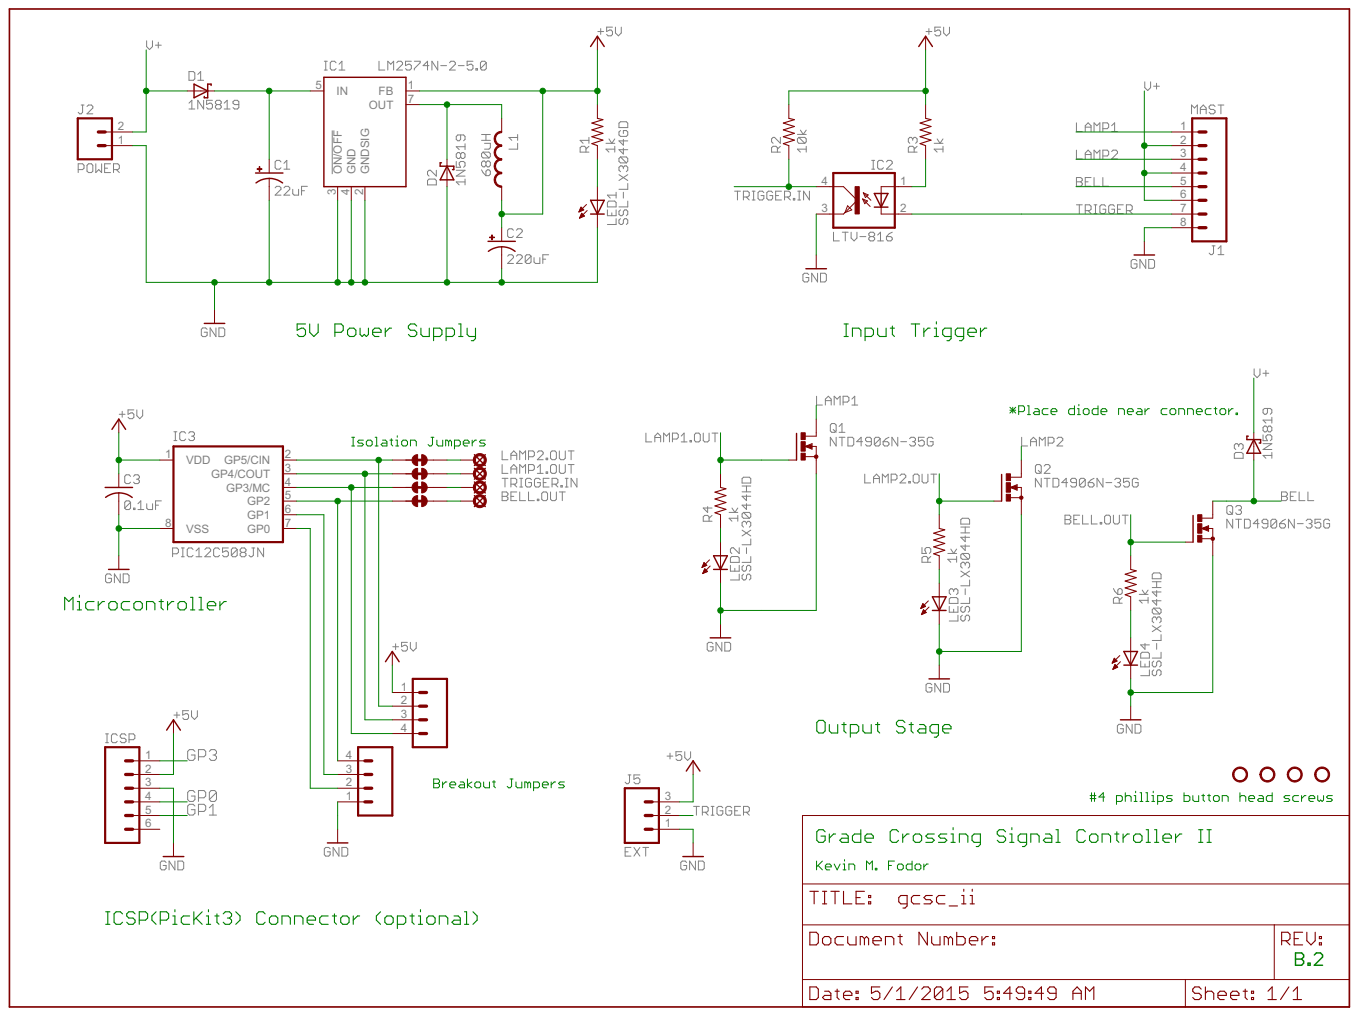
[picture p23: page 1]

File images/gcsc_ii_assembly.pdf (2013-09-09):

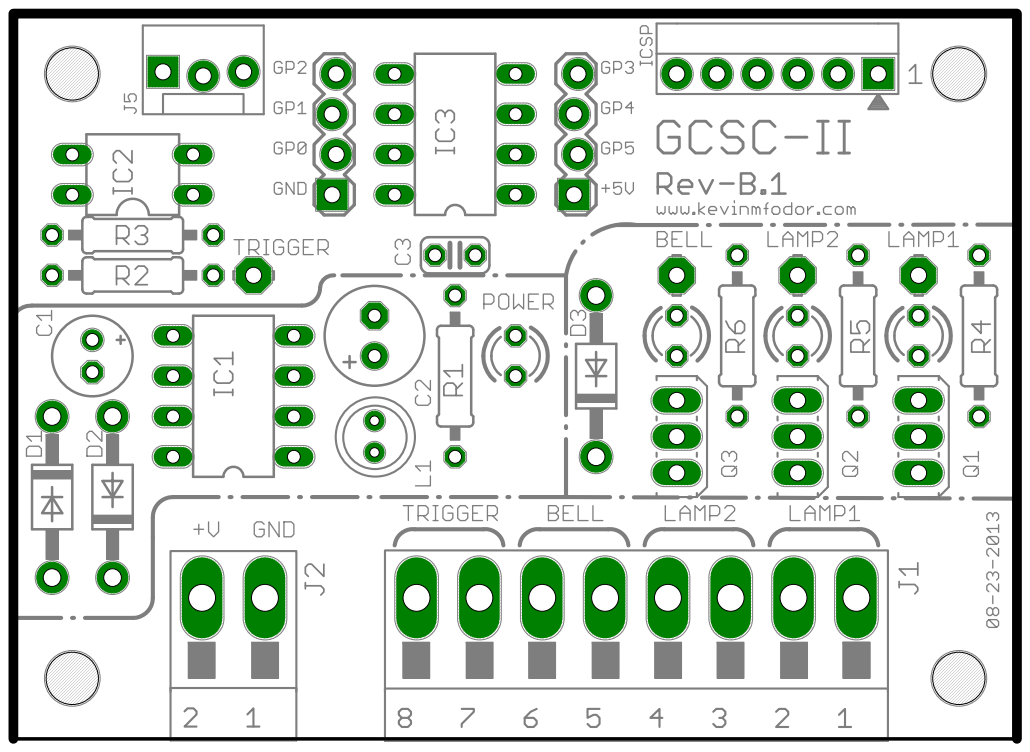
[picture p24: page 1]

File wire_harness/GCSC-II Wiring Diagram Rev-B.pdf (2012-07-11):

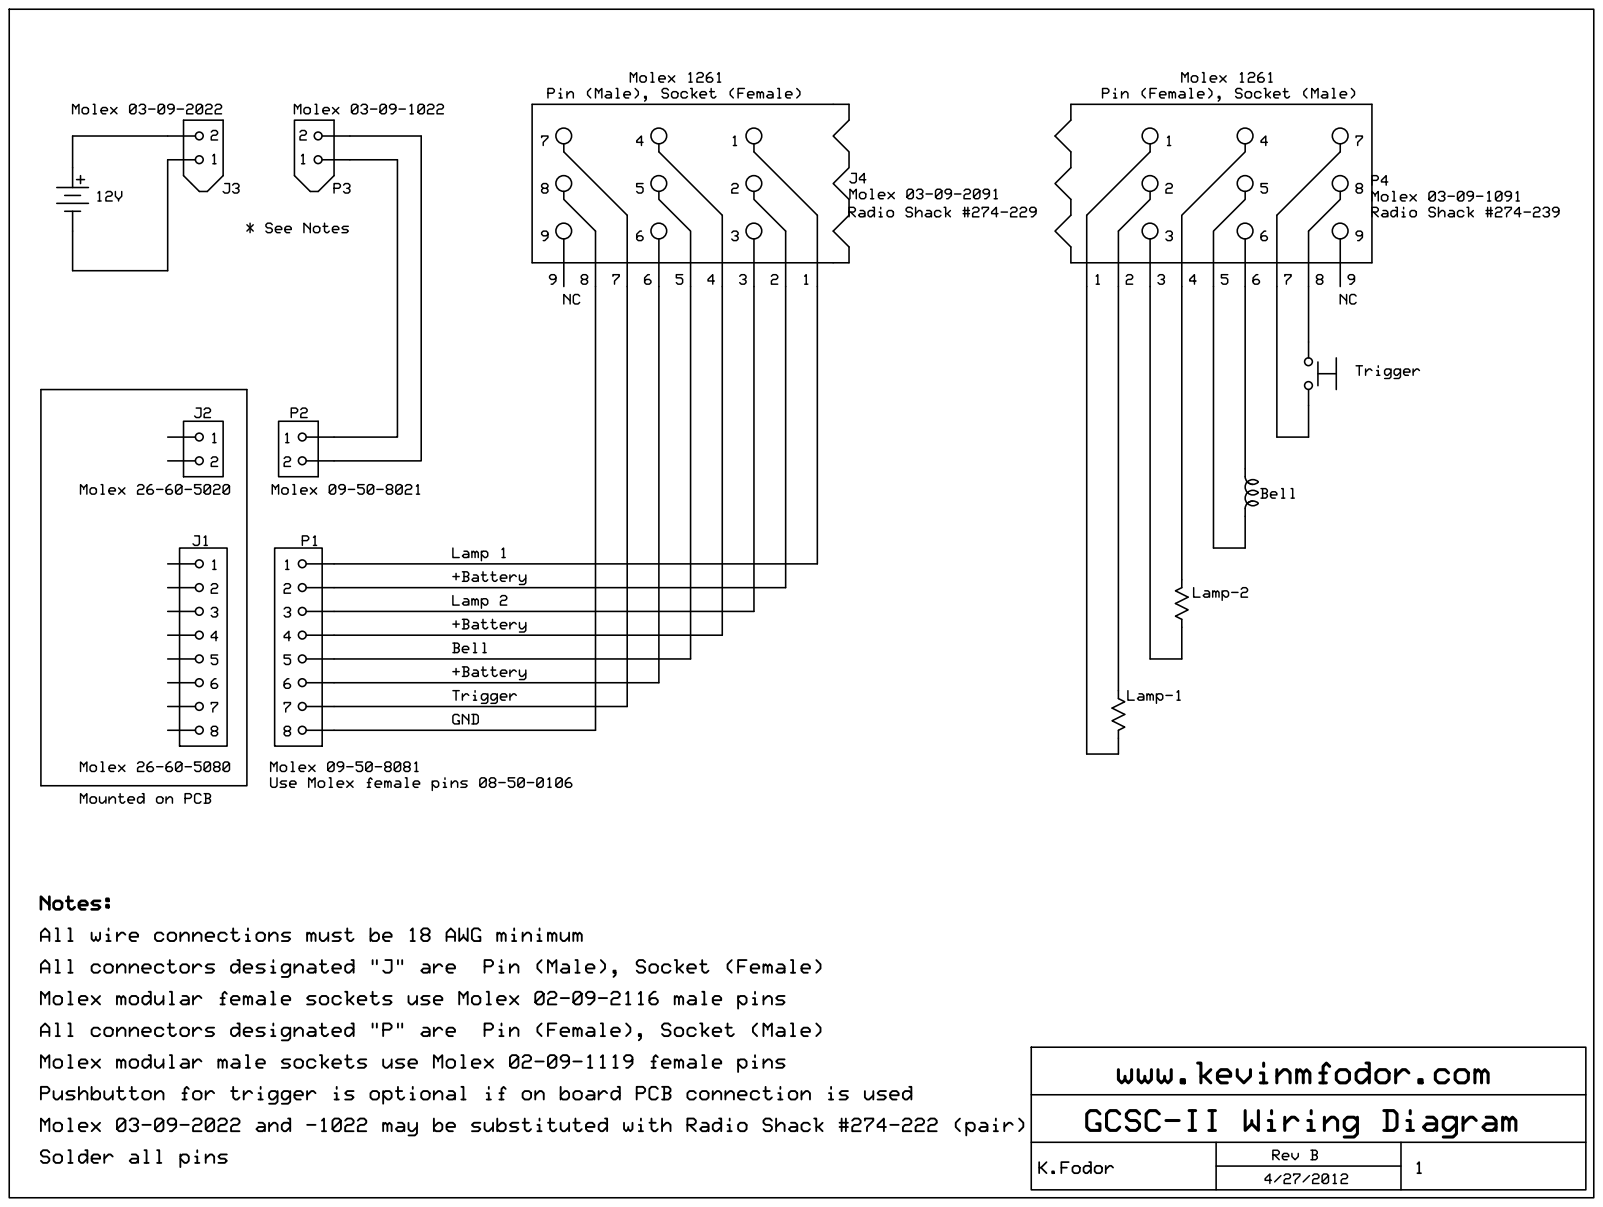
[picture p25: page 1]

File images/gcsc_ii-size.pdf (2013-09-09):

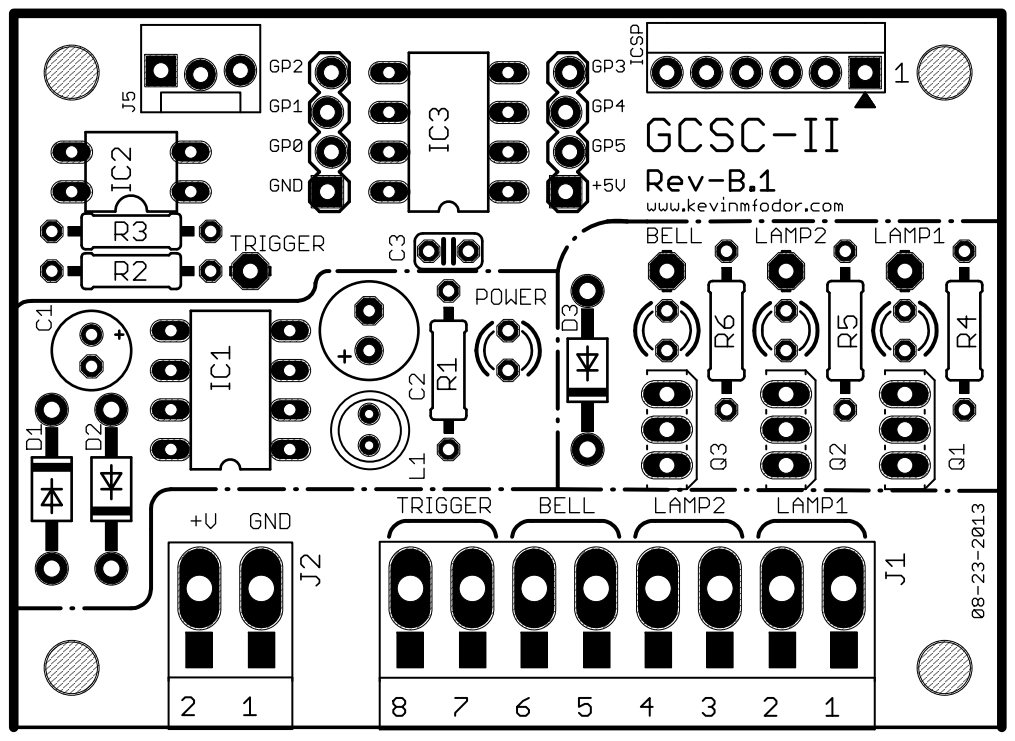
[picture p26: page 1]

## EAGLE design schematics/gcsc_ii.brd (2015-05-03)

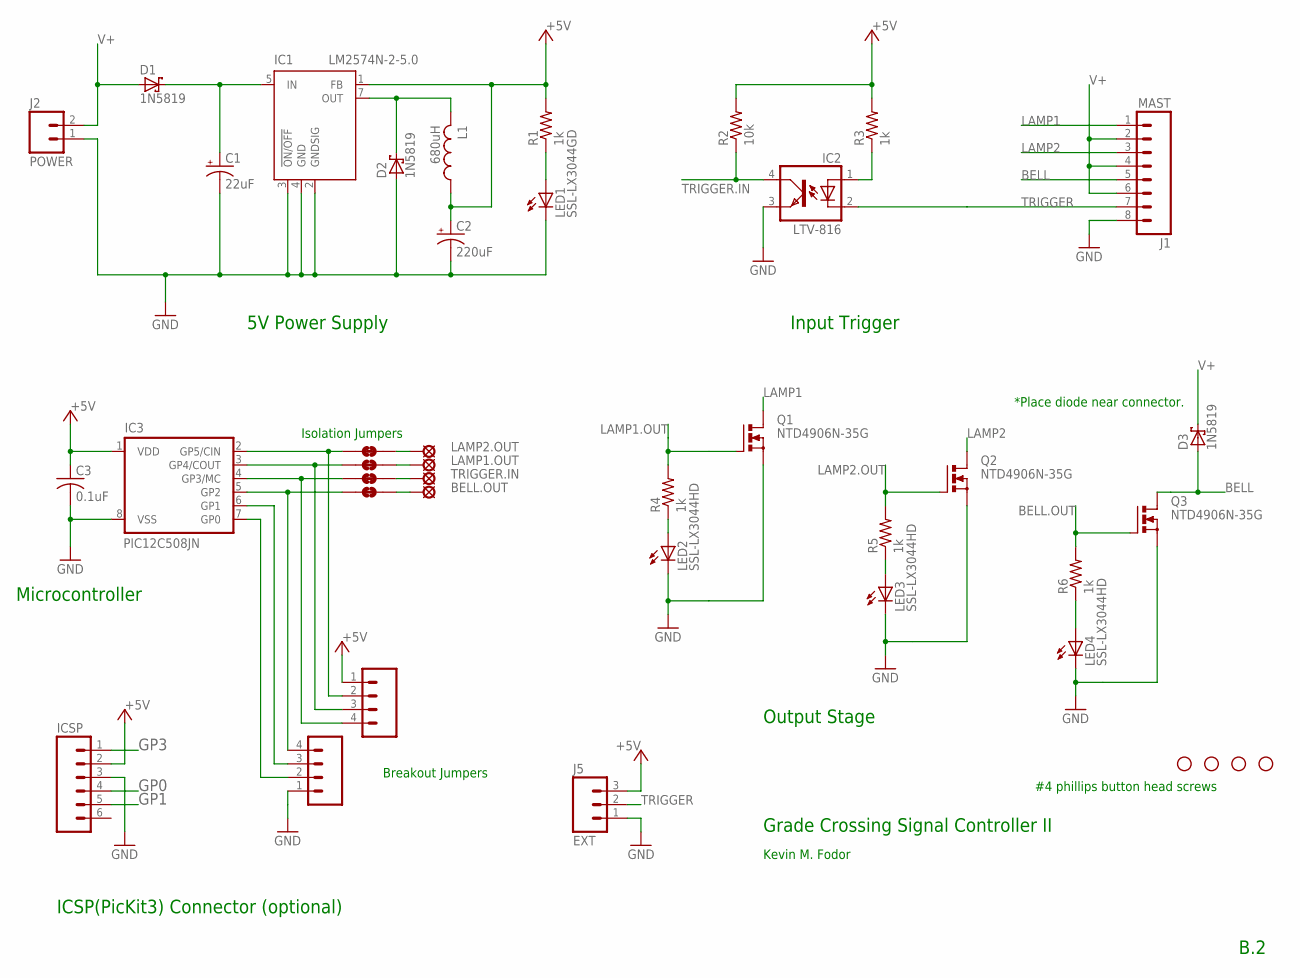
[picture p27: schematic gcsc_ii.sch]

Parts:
BELL.OUT: BELL; LSP10; PARTNO 22-28-4012
C1: 22uF; E2-5; PARTNO EEU-FR1H220
C2: 220uF; E2,5-6,3; PARTNO EEU-FR1C221
C3: 0.1uF; C025-024X044; PARTNO 21RZ310-RC
D1, D2, D3: 1N5819; DO41-10; PARTNO 1N5819
GP2: GP2; SJ_2S-TRACE
GP3: GP3; SJ_2S-TRACE
GP4: GP4; SJ_2S-TRACE
GP5: GP5; SJ_2S-TRACE
IC1: LM2574N-2-5.0; DIL8; PARTNO LM2574N-5G
IC2: LTV-816; DIL04; PARTNO LTV-816
IC3: PIC12C508JN; DIL8; MPN PIC12C508-04/P
ICSP: PIC_ICSP_RA; PIC_ICSP; PARTNO 68016-106HLF
J1: MAST; KK-156-8-RA; PARTNO 26-60-5080
J2: POWER; KK-156-2-RA; PARTNO 26-60-5020
J3: IC3_1-4; 1X04_LOCK; PARTNO 22-28-4042
J4: IC3_5-8; 1X04_LOCK; PARTNO 22-28-4042
J5: EXT; MOLEX-1X3_LOCK; PARTNO 22-27-2031
L1: 680uH; RLB0608; PARTNO RLB0608-681KL
LAMP1.OUT: LAMP1; LSP10; PARTNO 22-28-4012
LAMP2.OUT: LAMP2; LSP10; PARTNO 22-28-4012
LED1: SSL-LX3044GD; LED3MM; PARTNO SSL-LX3044GD
LED2, LED3, LED4: SSL-LX3044HD; LED3MM; PARTNO SSL-LX3044HD
Q1, Q2, Q3: NTD4906N-35G; I-PAK_STRAIGHT_LEAD; PARTNO NTD4906N-35G
R1, R3, R4, R5, R6: 1k; 0207/10; PARTNO 299-1K-RC
R2: 10k; 0207/10; PARTNO 299-10K-RC
TRIGGER.IN: TRIGGER; LSP10; PARTNO 22-28-4012
U$1, U$2, U$3, U$4: STAND-OFF

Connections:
+5V: C2.+, C3.1, IC1.1 (FB), IC3.1 (VDD), ICSP.2 (VDD), J3.1, J5.3, L1.1, R1.2, R2.2, R3.2
BELL: D3.A, J1.5, Q3.2 (D)
BELL.OUT: BELL.OUT.MP, GP2.2, Q3.1 (G), R6.2
GND: C1.-, C2.-, C3.2, D2.A, IC1.2 (GNDSIG), IC1.3 (!ON/OFF), IC1.4 (GND), IC2.3 (EMIT), IC3.8 (VSS), ICSP.3 (VSS), J1.8, J2.1, J4.1, J5.1, LED1.K (C), LED2.K (C), LED3.K (C), LED4.K (C), Q1.3 (S), Q2.3 (S), Q3.3 (S)
GP0: IC3.7 (GP0), ICSP.4 (ICSPDAT), J4.2
GP1: IC3.6 (GP1), ICSP.5 (ICSPCLK), J4.3
GP2: GP2.1, IC3.5 (GP2), J4.4
GP3: GP3.1, IC3.4 (GP3/MC), ICSP.1 (!MCLR), J3.4
GP4: GP4.1, IC3.3 (GP4/COUT), J3.3
GP5: GP5.1, IC3.2 (GP5/CIN), J3.2
LAMP1: J1.1, Q1.2 (D)
LAMP1.OUT: GP4.2, LAMP1.OUT.MP, Q1.1 (G), R4.2
LAMP2: J1.3, Q2.2 (D)
LAMP2.OUT: GP5.2, LAMP2.OUT.MP, Q2.1 (G), R5.2
unnamed: IC2.1 (A), R3.1
unnamed: LED1.A, R1.1
unnamed: C1.+, D1.C, IC1.5 (IN)
unnamed: D2.C, IC1.7 (OUT), L1.2
unnamed: LED2.A, R4.1
unnamed: LED3.A, R5.1
unnamed: LED4.A, R6.1
TRIGGER: IC2.2 (C), J1.7, J5.2
TRIGGER.IN: GP3.2, IC2.4 (COL), R2.1, TRIGGER.IN.MP
V+: D1.A, D3.C, J1.2, J1.4, J1.6, J2.2

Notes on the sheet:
#4 phillips button head screws
5V Power Supply
Grade Crossing Signal Controller II
Microcontroller
*Place diode near connector.
Input Trigger
Output Stage
ICSP(PicKit3) Connector (optional)
B.2
Kevin M. Fodor
Breakout Jumpers
Isolation Jumpers

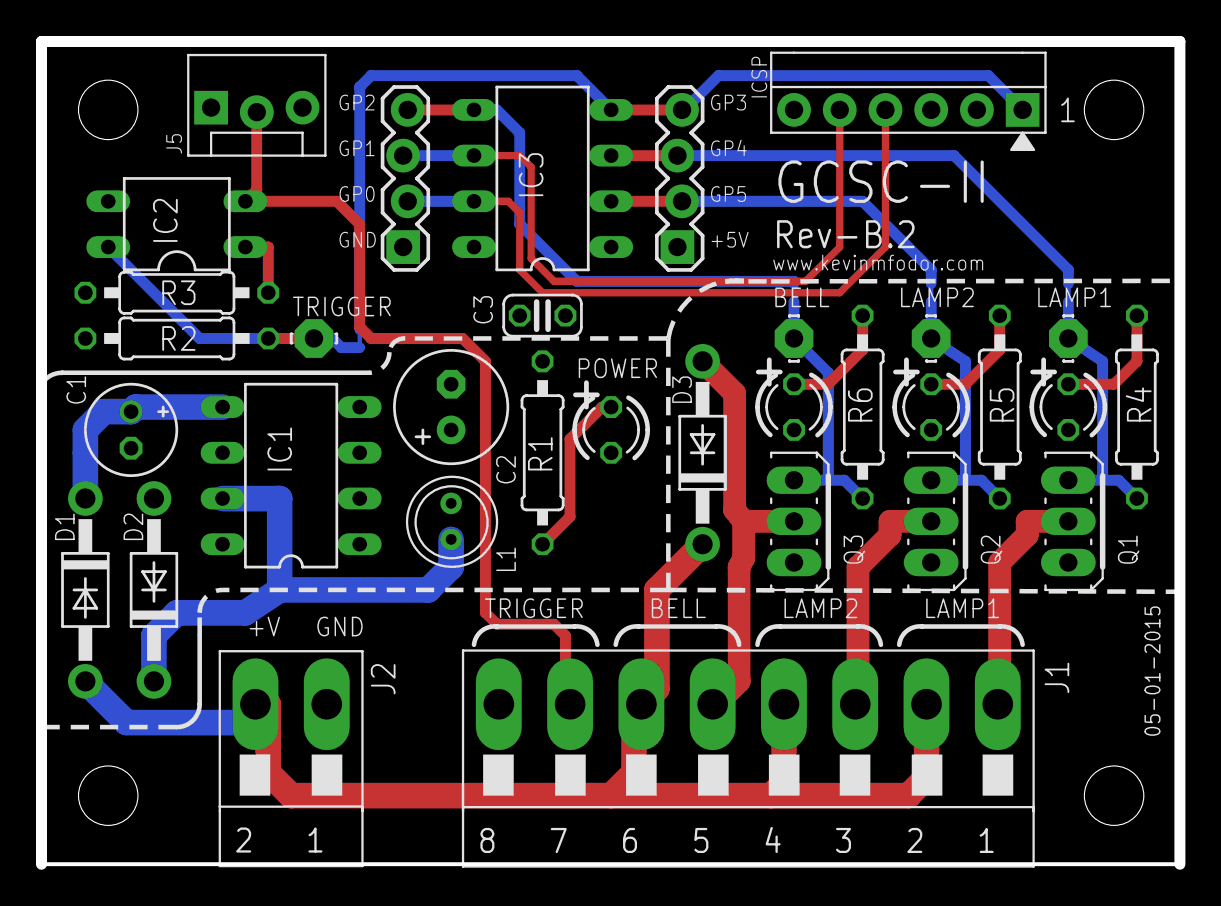
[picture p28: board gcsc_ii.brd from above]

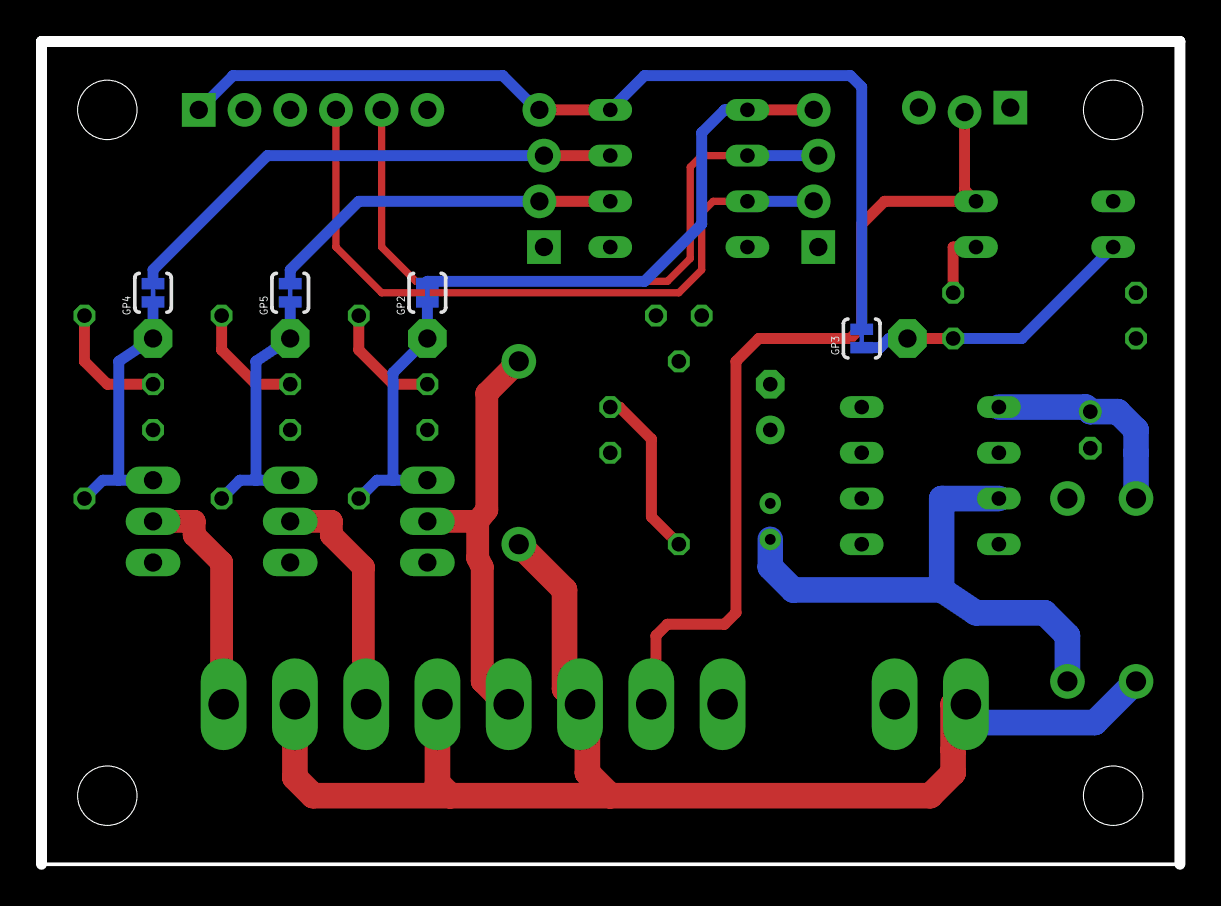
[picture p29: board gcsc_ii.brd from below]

Board: 2 copper layers, 63.2 x 45.7 mm, 41 parts (4 on the bottom side), 24 nets.

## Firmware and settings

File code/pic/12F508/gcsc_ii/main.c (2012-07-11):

/******************************************************************************/
/* Files to Include                                                           */
/******************************************************************************/

#include <htc.h>           /* Global Header File */
#include <stdint.h>        /* For uint8_t definition */
#include <stdbool.h>       /* For true/false definition */

#include "system.h"        /* System funct/params, like osc/peripheral config */
#include "user.h"          /* User funct/params, such as InitApp */

#include "gcsc_ii.h"

/******************************************************************************/
/* User Global Variable Declaration                                           */
/******************************************************************************/

/* i.e. uint8_t <variable_name>; */

/******************************************************************************/
/* Main Program                                                               */
/******************************************************************************/

uint8_t main(void)
{
    /* Configure the oscillator for the device */
    ConfigureOscillator();

    /* Initialize I/O and Peripherals for application */
    InitApp();

    /* Run Application */
    gcsc_ii();

    return 0;
}

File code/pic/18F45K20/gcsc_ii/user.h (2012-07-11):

/******************************************************************************/
/* User Level #define Macros                                                  */
/******************************************************************************/

/* TODO Application specific user parameters used in user.c may go here */

/******************************************************************************/
/* User Function Prototypes                                                   */
/******************************************************************************/

/* TODO User level functions prototypes (i.e. InitApp) go here */

#if _18F45K20 == 1

// Definitions for outputs (lamps, bell)
#define LAMP1       (0b00000001) // RD0
#define LAMP2       (0b00000010) // RD1
#define BELL        (0b00000100) // RD2
#define HEARTBEAT   (0b00001000) // RD3
#define PORT (LATD)

// Definitions for inputs
#define TRIGGER (PORTBbits.RB0 ? 0 : 1)

// Definitions for clock timer and delay
#define FOSC (31250)
#define TMR0_CLOCK_TICK_USEC ((4 * USEC_PER_SEC) / FOSC) // 128 usec
#define TMR0_COUNT (256 - (TMR0_TIMEOUT_USEC / TMR0_CLOCK_TICK_USEC)) // 178
#define USEC_PER_TICK ((256 - TMR0_COUNT) * TMR0_CLOCK_TICK_USEC) // 9984

#define TIMER_EXPIRED (INTCONbits.TMR0IF)
#define TIMER_RESET (TMR0L = TMR0_COUNT);INTCONbits.TMR0IF = 0

#else

#error Sorry! Incorrect header used for target chip.

#endif

void InitApp(void);         /* I/O and Peripheral Initialization */

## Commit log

2012-07-11 Initial files
    [GCSC-II Wiring Diagram Rev-B.sch, gcsc-ii.skp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]
2012-07-27 Added Make:Projects guide which explains how to build this PCB.
2013-08-23 Cleaned-up silk screen and some minor clean-up to traces.
    [gcsc_ii.brd, gcsc_ii.sch]
2013-08-28 Cleaned-up silkscreen, thickened traces. Electrically design is unaltered
    [gcsc_ii.brd, gcsc_ii.sch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]
2013-09-09 Updated PCB to Rev B.1 No changes to parts or design. Only some cleaning up of traces (thickening) and cosmetic improvements
    [gcsc_ii.brd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]
2015-05-03 Made slight modification to the top-silk to add heavier font for the "+" markings on the LEDs. Also updated to Eagle 6.6.0. Regenerated gerbers, schematic and archive.
    [gcsc_ii.brd, gcsc_ii.sch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]
